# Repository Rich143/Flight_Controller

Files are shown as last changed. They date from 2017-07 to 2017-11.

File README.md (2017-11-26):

 <a href="https://scan.coverity.com/projects/rich143-flight_controller">
  
</a>

# Flight Controller #

STM32 based flight controller for quadcopter

### Board Render:
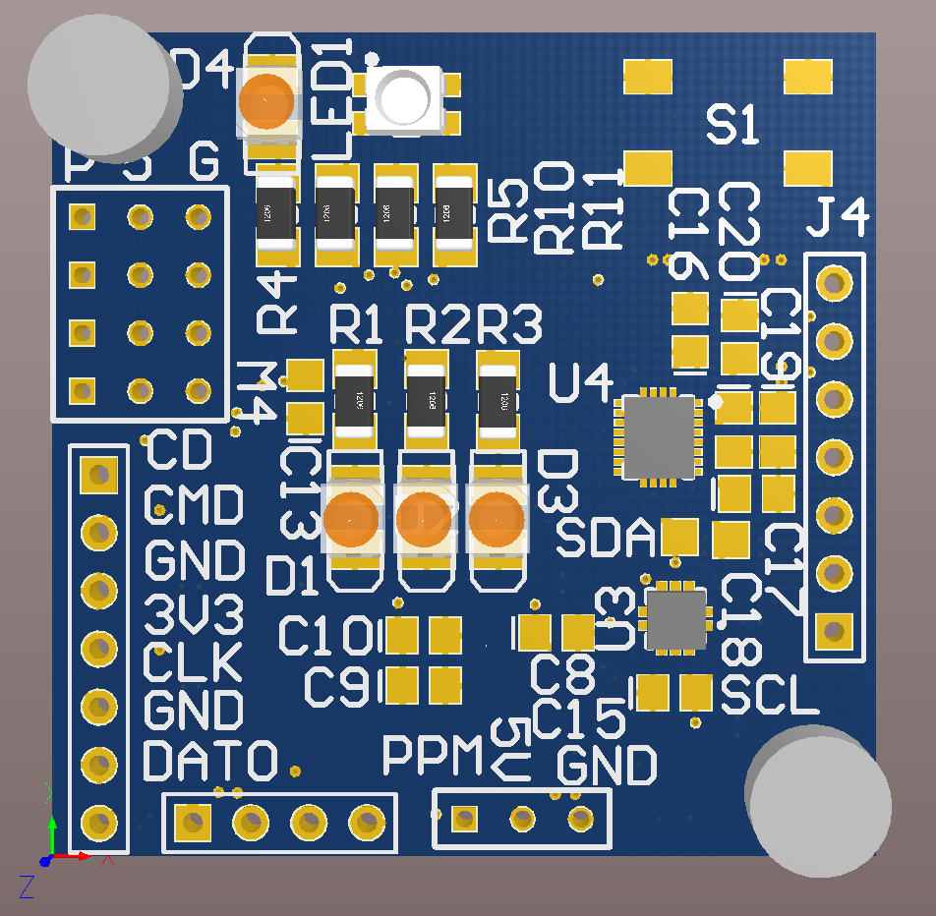
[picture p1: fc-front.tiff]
Board Render Front

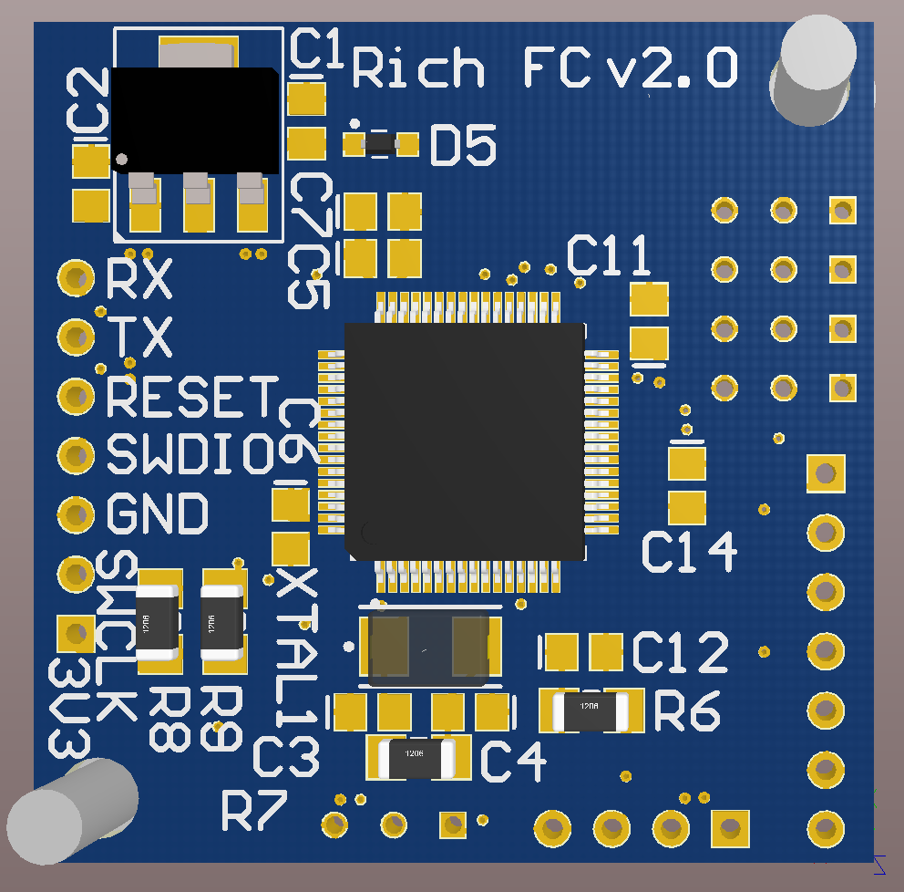
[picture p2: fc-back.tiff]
Board Render Back


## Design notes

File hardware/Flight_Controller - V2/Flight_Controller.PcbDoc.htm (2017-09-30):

Reporting Options

# File in Previous Format

Date | : | 9/21/2017
Time | : | 7:43:19 PM
Filename | : | C:\Users\Richard\Documents\Flight_Controller - V2\Flight_Controller.PcbDoc

Version | Warning

This file was generated by an earlier version of the software

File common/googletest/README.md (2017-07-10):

# Google Test #




Welcome to **Google Test**, Google's C++ test framework!

This repository is a merger of the formerly separate GoogleTest and
GoogleMock projects. These were so closely related that it makes sense to
maintain and release them together.

Please see the project page above for more information as well as the
mailing list for questions, discussions, and development.  There is
also an IRC channel on OFTC (irc.oftc.net) #gtest available.  Please
join us!

Getting started information for **Google Test** is available in the 
[Google Test Primer](googletest/docs/Primer.md) documentation.

**Google Mock** is an extension to Google Test for writing and using C++ mock
classes.  See the separate [Google Mock documentation](googlemock/README.md).

More detailed documentation for googletest (including build instructions) are
in its interior [googletest/README.md](googletest/README.md) file.

## Features ##

  * An [XUnit](https://en.wikipedia.org/wiki/XUnit) test framework.
  * Test discovery.
  * A rich set of assertions.
  * User-defined assertions.
  * Death tests.
  * Fatal and non-fatal failures.
  * Value-parameterized tests.
  * Type-parameterized tests.
  * Various options for running the tests.
  * XML test report generation.

## Platforms ##

Google test has been used on a variety of platforms:

  * Linux
  * Mac OS X
  * Windows
  * Cygwin
  * MinGW
  * Windows Mobile
  * Symbian

## Who Is Using Google Test? ##

In addition to many internal projects at Google, Google Test is also used by
the following notable projects:

  * The [Chromium projects](http://www.chromium.org/) (behind the Chrome
    browser and Chrome OS).
  * The [LLVM](http://llvm.org/) compiler.
  * [Protocol Buffers](https://github.com/google/protobuf), Google's data
    interchange format.
  * The [OpenCV](http://opencv.org/) computer vision library.

## Related Open Source Projects ##

[Google Test UI](https://github.com/ospector/gtest-gbar) is test runner that runs
your test binary, allows you to track its progress via a progress bar, and
displays a list of test failures. Clicking on one shows failure text. Google
Test UI is written in C#.

[GTest TAP Listener](https://github.com/kinow/gtest-tap-listener) is an event
listener for Google Test that implements the
[TAP protocol](https://en.wikipedia.org/wiki/Test_Anything_Protocol) for test
result output. If your test runner understands TAP, you may find it useful.

## Requirements ##

Google Test is designed to have fairly minimal requirements to build
and use with your projects, but there are some.  Currently, we support
Linux, Windows, Mac OS X, and Cygwin.  We will also make our best
effort to support other platforms (e.g. Solaris, AIX, and z/OS).
However, since core members of the Google Test project have no access
to these platforms, Google Test may have outstanding issues there.  If
you notice any problems on your platform, please notify
<googletestframework@googlegroups.com>. Patches for fixing them are
even more welcome!

### Linux Requirements ###

These are the base requirements to build and use Google Test from a source
package (as described below):

  * GNU-compatible Make or gmake
  * POSIX-standard shell
  * POSIX(-2) Regular Expressions (regex.h)
  * A C++98-standard-compliant compiler

### Windows Requirements ###

  * Microsoft Visual C++ v7.1 or newer

### Cygwin Requirements ###

  * Cygwin v1.5.25-14 or newer

### Mac OS X Requirements ###

  * Mac OS X v10.4 Tiger or newer
  * Xcode Developer Tools

### Requirements for Contributors ###

We welcome patches.  If you plan to contribute a patch, you need to
build Google Test and its own tests from a git checkout (described
below), which has further requirements:

  * [Python](https://www.python.org/) v2.3 or newer (for running some of
    the tests and re-generating certain source files from templates)
  * [CMake](https://cmake.org/) v2.6.4 or newer

## Regenerating Source Files ##

Some of Google Test's source files are generated from templates (not
in the C++ sense) using a script.
For example, the
file include/gtest/internal/gtest-type-util.h.pump is used to generate
gtest-type-util.h in the same directory.

You don't need to worry about regenerating the source files
unless you need to modify them.  You would then modify the
corresponding `.pump` files and run the '[pump.py](googletest/scripts/pump.py)'
generator script.  See the [Pump Manual](googletest/docs/PumpManual.md).

### Contributing Code ###

We welcome patches.  Please read the
[Developer's Guide](googletest/docs/DevGuide.md)
for how you can contribute. In particular, make sure you have signed
the Contributor License Agreement, or we won't be able to accept the
patch.

Happy testing!

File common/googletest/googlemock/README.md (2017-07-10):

## Google Mock ##

The Google C++ mocking framework.

### Overview ###

Google's framework for writing and using C++ mock classes.
It can help you derive better designs of your system and write better tests.

It is inspired by:

  * [jMock](http://www.jmock.org/),
  * [EasyMock](http://www.easymock.org/), and
  * [Hamcrest](http://code.google.com/p/hamcrest/),

and designed with C++'s specifics in mind.

Google mock:

  * lets you create mock classes trivially using simple macros.
  * supports a rich set of matchers and actions.
  * handles unordered, partially ordered, or completely ordered expectations.
  * is extensible by users.

We hope you find it useful!

### Features ###

  * Provides a declarative syntax for defining mocks.
  * Can easily define partial (hybrid) mocks, which are a cross of real
    and mock objects.
  * Handles functions of arbitrary types and overloaded functions.
  * Comes with a rich set of matchers for validating function arguments.
  * Uses an intuitive syntax for controlling the behavior of a mock.
  * Does automatic verification of expectations (no record-and-replay needed).
  * Allows arbitrary (partial) ordering constraints on
    function calls to be expressed,.
  * Lets a user extend it by defining new matchers and actions.
  * Does not use exceptions.
  * Is easy to learn and use.

Please see the project page above for more information as well as the
mailing list for questions, discussions, and development.  There is
also an IRC channel on OFTC (irc.oftc.net) #gtest available.  Please
join us!

Please note that code under [scripts/generator](scripts/generator/) is
from [cppclean](http://code.google.com/p/cppclean/) and released under
the Apache License, which is different from Google Mock's license.

## Getting Started ##

If you are new to the project, we suggest that you read the user
documentation in the following order:

  * Learn the [basics](../../master/googletest/docs/Primer.md) of
    Google Test, if you choose to use Google Mock with it (recommended).
  * Read [Google Mock for Dummies](../../master/googlemock/docs/ForDummies.md).
  * Read the instructions below on how to build Google Mock.

You can also watch Zhanyong's [talk](http://www.youtube.com/watch?v=sYpCyLI47rM) on Google Mock's usage and implementation.

Once you understand the basics, check out the rest of the docs:

  * [CheatSheet](../../master/googlemock/docs/CheatSheet.md) - all the commonly used stuff
    at a glance.
  * [CookBook](../../master/googlemock/docs/CookBook.md) - recipes for getting things done,
    including advanced techniques.

If you need help, please check the
[KnownIssues](docs/KnownIssues.md) and
[FrequentlyAskedQuestions](docs/FrequentlyAskedQuestions.md) before
posting a question on the
[discussion group](http://groups.google.com/group/googlemock).

### Using Google Mock Without Google Test ###

Google Mock is not a testing framework itself.  Instead, it needs a
testing framework for writing tests.  Google Mock works seamlessly
with [Google Test](http://code.google.com/p/googletest/), but
you can also use it with [any C++ testing framework](../../master/googlemock/docs/ForDummies.md#using-google-mock-with-any-testing-framework).

### Requirements for End Users ###

Google Mock is implemented on top of [Google Test](
http://github.com/google/googletest/), and depends on it.
You must use the bundled version of Google Test when using Google Mock.

You can also easily configure Google Mock to work with another testing
framework, although it will still need Google Test.  Please read
["Using_Google_Mock_with_Any_Testing_Framework"](
    ../../master/googlemock/docs/ForDummies.md#using-google-mock-with-any-testing-framework)
for instructions.

Google Mock depends on advanced C++ features and thus requires a more
modern compiler. The following are needed to use Google Mock:

#### Linux Requirements ####

  * GNU-compatible Make or "gmake"
  * POSIX-standard shell
  * POSIX(-2) Regular Expressions (regex.h)
  * C++98-standard-compliant compiler (e.g. GCC 3.4 or newer)

#### Windows Requirements ####

  * Microsoft Visual C++ 8.0 SP1 or newer

#### Mac OS X Requirements ####

  * Mac OS X 10.4 Tiger or newer
  * Developer Tools Installed

### Requirements for Contributors ###

We welcome patches. If you plan to contribute a patch, you need to
build Google Mock and its tests, which has further requirements:

  * Automake version 1.9 or newer
  * Autoconf version 2.59 or newer
  * Libtool / Libtoolize
  * Python version 2.3 or newer (for running some of the tests and
    re-generating certain source files from templates)

### Building Google Mock ###

If you have CMake available, it is recommended that you follow the
[build instructions][gtest_cmakebuild]
as described for Google Test. If are using Google Mock with an
existing CMake project, the section
[Incorporating Into An Existing CMake Project][gtest_incorpcmake]
may be of particular interest. Otherwise, the following sections
detail how to build Google Mock without CMake.

#### Preparing to Build (Unix only) ####

If you are using a Unix system and plan to use the GNU Autotools build
system to build Google Mock (described below), you'll need to
configure it now.

To prepare the Autotools build system:

    cd googlemock
    autoreconf -fvi

To build Google Mock and your tests that use it, you need to tell your
build system where to find its headers and source files.  The exact
way to do it depends on which build system you use, and is usually
straightforward.

This section shows how you can integrate Google Mock into your
existing build system.

Suppose you put Google Mock in directory `${GMOCK_DIR}` and Google Test
in `${GTEST_DIR}` (the latter is `${GMOCK_DIR}/gtest` by default).  To
build Google Mock, create a library build target (or a project as
called by Visual Studio and Xcode) to compile

    ${GTEST_DIR}/src/gtest-all.cc and ${GMOCK_DIR}/src/gmock-all.cc

with

    ${GTEST_DIR}/include and ${GMOCK_DIR}/include

in the system header search path, and

    ${GTEST_DIR} and ${GMOCK_DIR}

in the normal header search path.  Assuming a Linux-like system and gcc,
something like the following will do:

    g++ -isystem ${GTEST_DIR}/include -I${GTEST_DIR} \
        -isystem ${GMOCK_DIR}/include -I${GMOCK_DIR} \
        -pthread -c ${GTEST_DIR}/src/gtest-all.cc
    g++ -isystem ${GTEST_DIR}/include -I${GTEST_DIR} \
        -isystem ${GMOCK_DIR}/include -I${GMOCK_DIR} \
        -pthread -c ${GMOCK_DIR}/src/gmock-all.cc
    ar -rv libgmock.a gtest-all.o gmock-all.o

(We need -pthread as Google Test and Google Mock use threads.)

Next, you should compile your test source file with
${GTEST\_DIR}/include and ${GMOCK\_DIR}/include in the header search
path, and link it with gmock and any other necessary libraries:

    g++ -isystem ${GTEST_DIR}/include -isystem ${GMOCK_DIR}/include \
        -pthread path/to/your_test.cc libgmock.a -o your_test

As an example, the make/ directory contains a Makefile that you can
use to build Google Mock on systems where GNU make is available
(e.g. Linux, Mac OS X, and Cygwin).  It doesn't try to build Google
Mock's own tests.  Instead, it just builds the Google Mock library and
a sample test.  You can use it as a starting point for your own build
script.

If the default settings are correct for your environment, the
following commands should succeed:

    cd ${GMOCK_DIR}/make
    make
    ./gmock_test

If you see errors, try to tweak the contents of
[make/Makefile](make/Makefile) to make them go away.

### Windows ###

The msvc/2005 directory contains VC++ 2005 projects and the msvc/2010
directory contains VC++ 2010 projects for building Google Mock and
selected tests.

Change to the appropriate directory and run "msbuild gmock.sln" to
build the library and tests (or open the gmock.sln in the MSVC IDE).
If you want to create your own project to use with Google Mock, you'll
have to configure it to use the `gmock_config` propety sheet.  For that:

 * Open the Property Manager window (View | Other Windows | Property Manager)
 * Right-click on your project and select "Add Existing Property Sheet..."
 * Navigate to `gmock_config.vsprops` or `gmock_config.props` and select it.
 * In Project Properties | Configuration Properties | General | Additional
   Include Directories, type <path to Google Mock>/include.

### Tweaking Google Mock ###

Google Mock can be used in diverse environments.  The default
configuration may not work (or may not work well) out of the box in
some environments.  However, you can easily tweak Google Mock by
defining control macros on the compiler command line.  Generally,
these macros are named like `GTEST_XYZ` and you define them to either 1
or 0 to enable or disable a certain feature.

We list the most frequently used macros below.  For a complete list,
see file [${GTEST\_DIR}/include/gtest/internal/gtest-port.h](
../googletest/include/gtest/internal/gtest-port.h).

### Choosing a TR1 Tuple Library ###

Google Mock uses the C++ Technical Report 1 (TR1) tuple library
heavily.  Unfortunately TR1 tuple is not yet widely available with all
compilers.  The good news is that Google Test 1.4.0+ implements a
subset of TR1 tuple that's enough for Google Mock's need.  Google Mock
will automatically use that implementation when the compiler doesn't
provide TR1 tuple.

Usually you don't need to care about which tuple library Google Test
and Google Mock use.  However, if your project already uses TR1 tuple,
you need to tell Google Test and Google Mock to use the same TR1 tuple
library the rest of your project uses, or the two tuple
implementations will clash.  To do that, add

    -DGTEST_USE_OWN_TR1_TUPLE=0

to the compiler flags while compiling Google Test, Google Mock, and
your tests.  If you want to force Google Test and Google Mock to use
their own tuple library, just add

    -DGTEST_USE_OWN_TR1_TUPLE=1

to the compiler flags instead.

If you want to use Boost's TR1 tuple library with Google Mock, please
refer to the Boost website (http://www.boost.org/) for how to obtain
it and set it up.

### As a Shared Library (DLL) ###

Google Mock is compact, so most users can build and link it as a static
library for the simplicity.  Google Mock can be used as a DLL, but the
same DLL must contain Google Test as well.  See
[Google Test's README][gtest_readme]
for instructions on how to set up necessary compiler settings.

### Tweaking Google Mock ###

Most of Google Test's control macros apply to Google Mock as well.
Please see [Google Test's README][gtest_readme] for how to tweak them.

### Upgrading from an Earlier Version ###

We strive to keep Google Mock releases backward compatible.
Sometimes, though, we have to make some breaking changes for the
users' long-term benefits.  This section describes what you'll need to
do if you are upgrading from an earlier version of Google Mock.

#### Upgrading from 1.1.0 or Earlier ####

You may need to explicitly enable or disable Google Test's own TR1
tuple library.  See the instructions in section "[Choosing a TR1 Tuple
Library](../googletest/#choosing-a-tr1-tuple-library)".

#### Upgrading from 1.4.0 or Earlier ####

On platforms where the pthread library is available, Google Test and
Google Mock use it in order to be thread-safe.  For this to work, you
may need to tweak your compiler and/or linker flags.  Please see the
"[Multi-threaded Tests](../googletest#multi-threaded-tests
)" section in file Google Test's README for what you may need to do.

If you have custom matchers defined using `MatcherInterface` or
`MakePolymorphicMatcher()`, you'll need to update their definitions to
use the new matcher API (
[monomorphic](http://code.google.com/p/googlemock/wiki/CookBook#Writing_New_Monomorphic_Matchers),
[polymorphic](http://code.google.com/p/googlemock/wiki/CookBook#Writing_New_Polymorphic_Matchers)).
Matchers defined using `MATCHER()` or `MATCHER_P*()` aren't affected.

### Developing Google Mock ###

This section discusses how to make your own changes to Google Mock.

#### Testing Google Mock Itself ####

To make sure your changes work as intended and don't break existing
functionality, you'll want to compile and run Google Test's own tests.
For that you'll need Autotools.  First, make sure you have followed
the instructions above to configure Google Mock.
Then, create a build output directory and enter it.  Next,

    ${GMOCK_DIR}/configure  # try --help for more info

Once you have successfully configured Google Mock, the build steps are
standard for GNU-style OSS packages.

    make        # Standard makefile following GNU conventions
    make check  # Builds and runs all tests - all should pass.

Note that when building your project against Google Mock, you are building
against Google Test as well.  There is no need to configure Google Test
separately.

#### Contributing a Patch ####

We welcome patches.
Please read the [Developer's Guide](docs/DevGuide.md)
for how you can contribute. In particular, make sure you have signed
the Contributor License Agreement, or we won't be able to accept the
patch.

Happy testing!

[gtest_readme]: ../googletest/README.md "googletest"
[gtest_cmakebuild]:  ../googletest/README.md#using-cmake "Using CMake"
[gtest_incorpcmake]: ../googletest/README.md#incorporating-into-an-existing-cmake-project "Incorporating Into An Existing CMake Project"

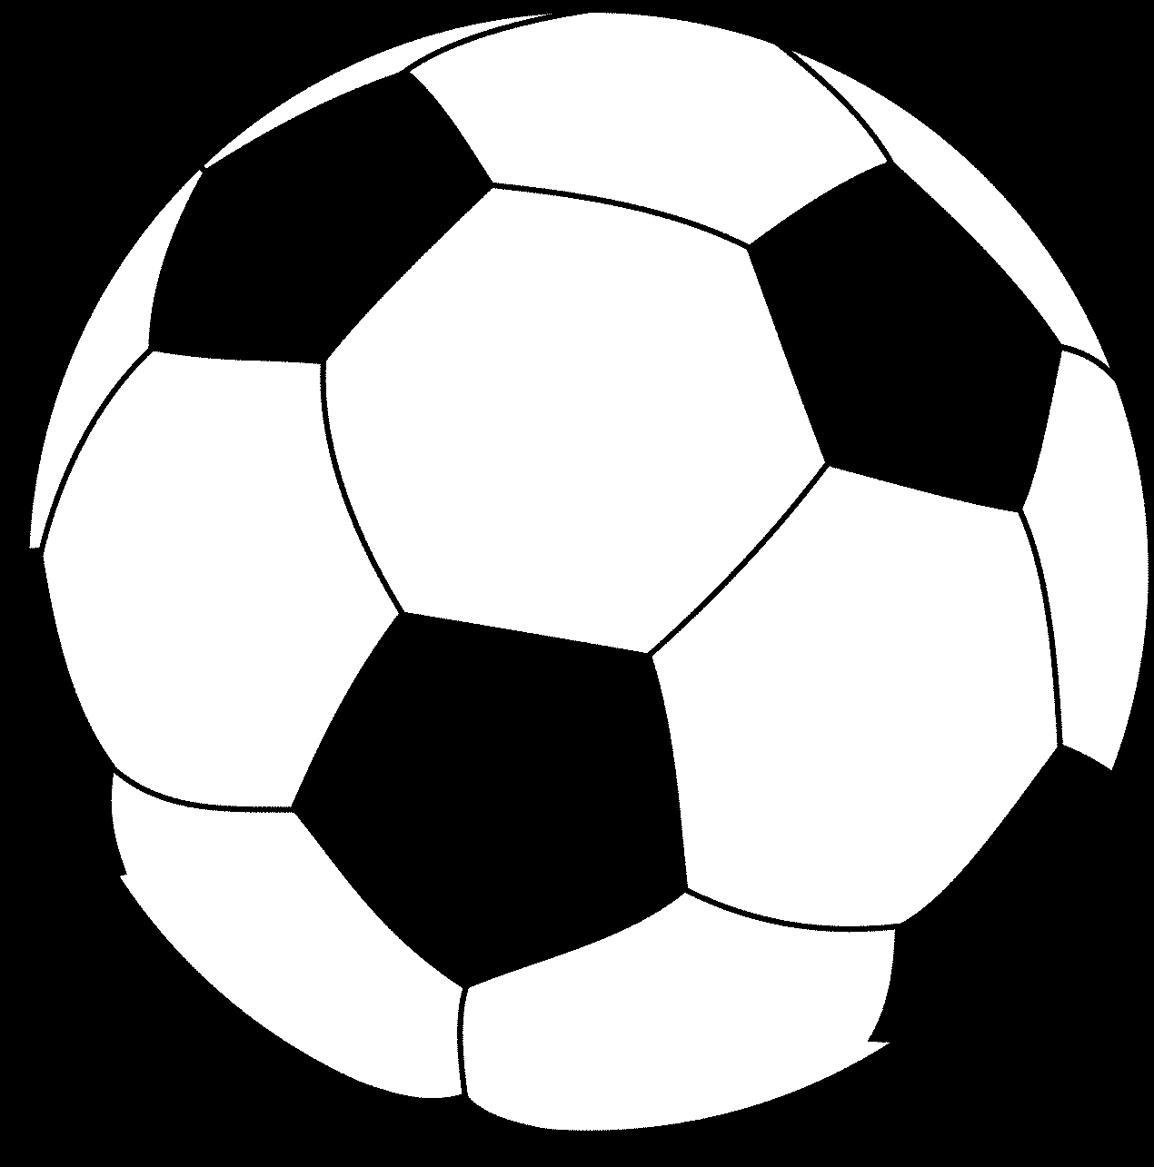
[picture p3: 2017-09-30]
hardware/Flight_Controller - V2/Soccerball.bmp

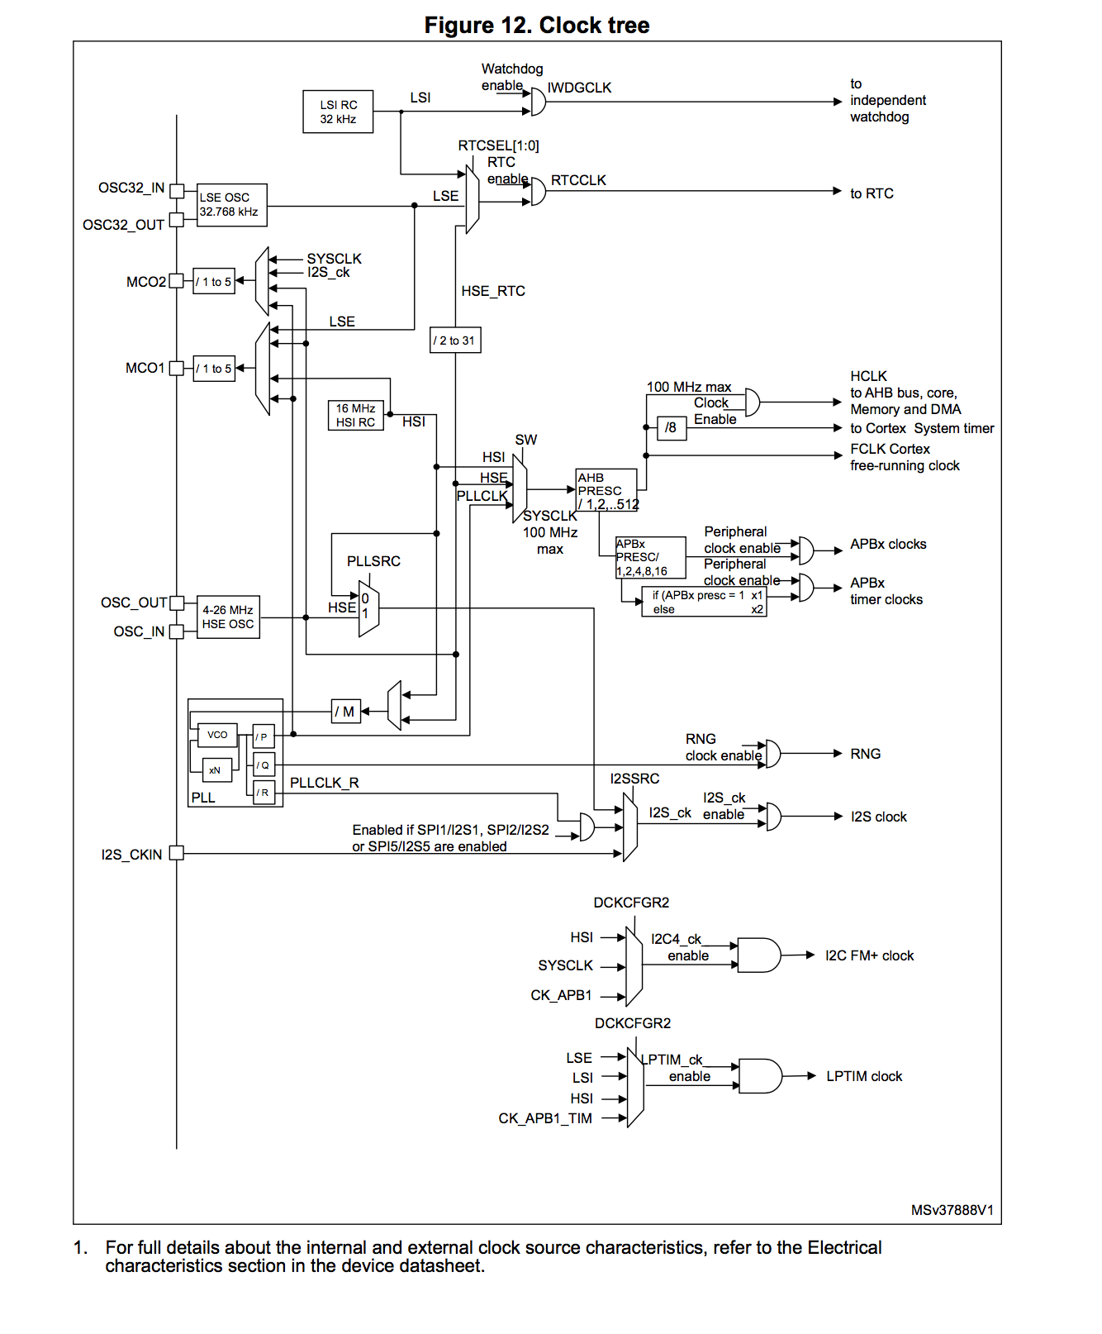
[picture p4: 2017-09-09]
docs/clock-tree.tiff

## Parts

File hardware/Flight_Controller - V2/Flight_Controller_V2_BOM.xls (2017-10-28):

Comment | Description | Designator | Footprint | LibRef | Quantity | Supplier 1 | Supplier Unit Price 1 | Supplier Currency 1 | Supplier Part Number 1 | Supplier Stock 1 | Value
Cap | Capacitor | C1, C2, C19 | C0805 | Cap | 3.0 |  | 0.0 |  |  | 0.0 | 10uF
Cap | Capacitor | C3, C4 | C0805 | Cap | 2.0 |  | 0.0 |  |  | 0.0 | 8pF
Cap | Capacitor | C5, C6, C8, C10, C11, C12, C14, C15, C16, C18, C20 | C0805 | Cap | 11.0 |  | 0.0 |  |  | 0.0 | 100nF
Cap | Capacitor | C7, C13 | C0805 | Cap | 2.0 |  | 0.0 |  |  | 0.0 | 4.7uF
Cap | Capacitor | C9 | C0805 | Cap | 1.0 |  | 0.0 |  |  | 0.0 | 1uF
Cap | Capacitor | C17 | C0805 | Cap | 1.0 |  | 0.0 |  |  | 0.0 | 10nF
150141GS73100 | Typical GREEN LED | D1 | 150141RS73100 | 150141GS73100 | 1.0 | Digikey | 0.2133 | CAD | 732-4997-1-ND | 7703.0
150141RS73100 | Typical RED LED | D2, D3, D4 | 150141RS73100 | 150141RS73100 | 3.0 | Digi-Key | 0.0 |  |  | 0.0
Schottky Diode | Diode Schottky 30V 800mA (DC) Surface Mount SOD-323 | D5 | SOD323 | DS_CUS08F30 | 1.0 | Digi-Key | 0.4517 | CAD | CUS08F30H3FCT-ND | 49875.0
Header_3x1 |  | J1 | Header_3x1 | Header_3x1 | 1.0 |  | 0.0 |  |  | 0.0
Header 4x3 |  | J2 | Header_4x3 | Header_4x3 | 1.0 |  | 0.0 |  |  | 0.0
Header 4 | Header, 4-Pin | J3 | HDR1X4 | Header 4 | 1.0 |  | 0.0 |  |  | 0.0
Header 7 | Header, 7-Pin | J4, P1 | HDR1X7 | Header 7 | 2.0 |  | 0.0 |  |  | 0.0
RGB | Wurth RGB LED 1411 pkg | LED1 | 1411LED | LED_150141M173100 | 1.0 | Digi-Key | 0.56462 | CAD | 732-4998-1-ND | 7499.0
M3_Mounting_Hole |  | M1, M2 | M3_Mounting_Hole | M3_Mounting_Hole | 2.0 |  | 0.0 |  |  | 0.0
Res | Surface Mount Resistor | R1, R2, R3, R4, R5, R6, R10, R11 | 3216[1206] | Res | 8.0 |  | 0.0 |  |  | 0.0 | 1K
Res | Surface Mount Resistor | R7 | 3216[1206] | Res | 1.0 |  | 0.0 |  |  | 0.0 | 640
Res | Surface Mount Resistor | R8, R9 | 3216[1206] | Res | 2.0 |  | 0.0 |  |  | 0.0 | 4.7k
Pushbutton |  | S1 | TactileSwitch | Pushbutton | 1.0 |  | 0.0 |  |  | 0.0
Test_point_SMD | Test Point SMD | TPS1, TPS2 | TEST_POINT_SMD | Test_point_SMD | 2.0 |  | 0.0 |  |  | 0.0
U_AZ1117EH-3.3TRG1 | IC LDO 3.3V 1A | U1 | SOT223 | U_AZ1117EH-3.3TRG1 | 1.0 | Digi-Key | 0.53953 | CAD | AZ1117EH-3.3TRG1DICT-ND | 103155.0
STM32F410RBT6 | 64-LQFP - Pinout Representation | U2 | LQFP-64 10x10mm | STM32F410RB_PINOUT | 1.0 | Digikey | 5.52076 | CAD | 497-16239-ND | 0.0
LPS25HB |  | U3 | HLGA-10L - narrow | LPS25HB | 1.0 | Digikey | 4.07784 | CAD | 497-15070-6-ND | 40076.0
LSM9DS1 |  | U4 | LGA-24 - NARROW - Long Pads | LSM9DS1 | 1.0 | Digikey | 8.0302 | CAD | 497-14946-6-ND | 0.0
NX5032GA 25MHz | NX5032GA | XTAL1 | NX5032GA | NX5032GA | 1.0 | Digikey | 0.82811 | CAD | 644-1041-1-ND | 0.0

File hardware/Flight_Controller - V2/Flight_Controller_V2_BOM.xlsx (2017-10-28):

 |  | Comment | Description | Designator | Footprint | LibRef | Quantity | Supplier 1 | Supplier Unit Price 1 | Supplier Currency 1 | Supplier Part Number 1 | Supplier Stock 1 | Value | Used | Remaining
 | T,B | Cap | Capacitor | C1, C2, C19 | C0805 | Cap | 3 |  | 0 |  |  | 0 | 10uF | 7 | 3
 | T,B | Cap | Capacitor | C3, C4 | C0805 | Cap | 2 |  | 0 |  |  | 0 | 8pF | 4 | 6
c8,c10,c15,c16,c18,c20 | c5,c6,c11,c12,c14 | Cap | Capacitor | C5, C6, C8, C10, C11, C12, C14, C15, C16, C18, C20 | C0805 | Cap | 11 |  | 0 |  |  | 0 | 100nF | 22 | 78
c13, | c7, | Cap | Capacitor | C7, C13 | C0805 | Cap | 2 |  | 0 |  |  | 0 | 4.7uF | 4 | 6
c9 |  | Cap | Capacitor | C9 | C0805 | Cap | 1 |  | 0 |  |  | 0 | 1uF | 2 | 8
c17 |  | Cap | Capacitor | C17 | C0805 | Cap | 1 |  | 0 |  |  | 0 | 10nF | 2 | 8
d1 |  | 150141GS73100 | Typical GREEN LED | D1 | 150141RS73100 | 150141GS73100 | 1 | Digikey | 0.2133 | CAD | 732-4997-1-ND | 7703 |  | 2 | 1
d2,d3,d4 |  | 150141RS73100 | Typical RED LED | D2, D3, D4 | 150141RS73100 | 150141RS73100 | 3 | Digi-Key | 0 |  |  | 0 |  | 7 | 5
d5 |  | Schottky Diode | Diode Schottky 30V 800mA (DC) Surface Mount SOD-323 | D5 | SOD323 | DS_CUS08F30 | 1 | Digi-Key | 0.4517 | CAD | CUS08F30H3FCT-ND | 49875 |  | 1 | 2
 |  | Header_3x1 |  | J1 | Header_3x1 | Header_3x1 | 1 |  | 0 |  |  | 0
 |  | Header 4x3 |  | J2 | Header_4x3 | Header_4x3 | 1 |  | 0 |  |  | 0
 |  | Header 4 | Header, 4-Pin | J3 | HDR1X4 | Header 4 | 1 |  | 0 |  |  | 0
 |  | Header 7 | Header, 7-Pin | J4, P1 | HDR1X7 | Header 7 | 2 |  | 0 |  |  | 0
led1 |  | RGB | Wurth RGB LED 1411 pkg | LED1 | 1411LED | LED_150141M173100 | 1 | Digi-Key | 0.56462 | CAD | 732-4998-1-ND | 7499 |  | 1 | 1
 |  | M3_Mounting_Hole |  | M1, M2 | M3_Mounting_Hole | M3_Mounting_Hole | 2 |  | 0 |  |  | 0
r1,r2,r3,r4,r5,r10,r11 | r6, | Res | Surface Mount Resistor | R1, R2, R3, R4, R5, R6, R10, R11 | 3216[1206] | Res | 8 |  | 0 |  |  | 0 | 1K | 16 | 9
 | r7 | Res | Surface Mount Resistor | R7 | 3216[1206] | Res | 1 |  | 0 |  |  | 0 | 640 | 2 | 8
 | r8,r9 | Res | Surface Mount Resistor | R8, R9 | 3216[1206] | Res | 2 |  | 0 |  |  | 0 | 4.7k | 4 | 6
 | s1 | Pushbutton |  | S1 | TactileSwitch | Pushbutton | 1 |  | 0 |  |  | 0
 |  | Test_point_SMD | Test Point SMD | TPS1, TPS2 | TEST_POINT_SMD | Test_point_SMD | 2 |  | 0 |  |  | 0
 | u1 | U_AZ1117EH-3.3TRG1 | IC LDO 3.3V 1A | U1 | SOT223 | U_AZ1117EH-3.3TRG1 | 1 | Digi-Key | 0.53953 | CAD | AZ1117EH-3.3TRG1DICT-ND | 103155 |  | 2 | 2
 |  | STM32F410RBT6 | 64-LQFP - Pinout Representation | U2 | LQFP-64 10x10mm | STM32F410RB_PINOUT | 1 | Digikey | 5.52076 | CAD | 497-16239-ND | 0
 |  | LPS25HB |  | U3 | HLGA-10L - narrow | LPS25HB | 1 | Digikey | 4.07784 | CAD | 497-15070-6-ND | 40076
 |  | LSM9DS1 |  | U4 | LGA-24 - NARROW - Long Pads | LSM9DS1 | 1 | Digikey | 8.0302 | CAD | 497-14946-6-ND | 0
 | xtal1 | NX5032GA 25MHz | NX5032GA | XTAL1 | NX5032GA | NX5032GA | 1 | Digikey | 0.82811 | CAD | 644-1041-1-ND | 0

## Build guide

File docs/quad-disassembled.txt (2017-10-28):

Steps taken to disassemble quad for testing:
-took off top plate
-cut off zip tie holding antenna in place
-unplugged rc connector from receiver to fc, goes in pins on top from unlabelled, circle, and pin with label 1
-unplugged esc connectors from fc, goes into first for from front, in order back right, front right, back left, front left
-unplugged vtx connector
-unplugged batt monitor, purple cable that goes to +Batt
-unplugged beeper, blue cable goes to plus side, adjacent to batt monitor, green goes to minus side
-spare parts in container in workbench

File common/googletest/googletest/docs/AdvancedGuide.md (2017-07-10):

Now that you have read [Primer](Primer.md) and learned how to write tests
using Google Test, it's time to learn some new tricks. This document
will show you more assertions as well as how to construct complex
failure messages, propagate fatal failures, reuse and speed up your
test fixtures, and use various flags with your tests.

# More Assertions #

This section covers some less frequently used, but still significant,
assertions.

## Explicit Success and Failure ##

These three assertions do not actually test a value or expression. Instead,
they generate a success or failure directly. Like the macros that actually
perform a test, you may stream a custom failure message into the them.

| `SUCCEED();` |
|:-------------|

Generates a success. This does NOT make the overall test succeed. A test is
considered successful only if none of its assertions fail during its execution.

Note: `SUCCEED()` is purely documentary and currently doesn't generate any
user-visible output. However, we may add `SUCCEED()` messages to Google Test's
output in the future.

| `FAIL();`  | `ADD_FAILURE();` | `ADD_FAILURE_AT("`_file\_path_`", `_line\_number_`);` |
|:---|:---|:---|

`FAIL()` generates a fatal failure, while `ADD_FAILURE()` and `ADD_FAILURE_AT()` generate a nonfatal
failure. These are useful when control flow, rather than a Boolean expression,
deteremines the test's success or failure. For example, you might want to write
something like:

```
switch(expression) {
  case 1: ... some checks ...
  case 2: ... some other checks
  ...
  default: FAIL() << "We shouldn't get here.";
}
```

Note: you can only use `FAIL()` in functions that return `void`. See the [Assertion Placement section](#assertion-placement) for more information.

_Availability_: Linux, Windows, Mac.

## Exception Assertions ##

These are for verifying that a piece of code throws (or does not
throw) an exception of the given type:

| **Fatal assertion** | **Nonfatal assertion** | **Verifies** |
|:---|:---|:---|
| `ASSERT_THROW(`_statement_, _exception\_type_`);`  | `EXPECT_THROW(`_statement_, _exception\_type_`);`  | _statement_ throws an exception of the given type  |
| `ASSERT_ANY_THROW(`_statement_`);` | `EXPECT_ANY_THROW(`_statement_`);` | _statement_ throws an exception of any type |
| `ASSERT_NO_THROW(`_statement_`);` | `EXPECT_NO_THROW(`_statement_`);` | _statement_ doesn't throw any exception |

Examples:

```
ASSERT_THROW(Foo(5), bar_exception);

EXPECT_NO_THROW({
  int n = 5;
  Bar(&n);
});
```

_Availability_: Linux, Windows, Mac; since version 1.1.0.

## Predicate Assertions for Better Error Messages ##

Even though Google Test has a rich set of assertions, they can never be
complete, as it's impossible (nor a good idea) to anticipate all the scenarios
a user might run into. Therefore, sometimes a user has to use `EXPECT_TRUE()`
to check a complex expression, for lack of a better macro. This has the problem
of not showing you the values of the parts of the expression, making it hard to
understand what went wrong. As a workaround, some users choose to construct the
failure message by themselves, streaming it into `EXPECT_TRUE()`. However, this
is awkward especially when the expression has side-effects or is expensive to
evaluate.

Google Test gives you three different options to solve this problem:

### Using an Existing Boolean Function ###

If you already have a function or a functor that returns `bool` (or a type
that can be implicitly converted to `bool`), you can use it in a _predicate
assertion_ to get the function arguments printed for free:

| **Fatal assertion** | **Nonfatal assertion** | **Verifies** |
|:---|:---|:---|
| `ASSERT_PRED1(`_pred1, val1_`);` | `EXPECT_PRED1(`_pred1, val1_`);` | _pred1(val1)_ returns true |
| `ASSERT_PRED2(`_pred2, val1, val2_`);` | `EXPECT_PRED2(`_pred2, val1, val2_`);` |  _pred2(val1, val2)_ returns true |
|  ... | ... | ... |

In the above, _predn_ is an _n_-ary predicate function or functor, where
_val1_, _val2_, ..., and _valn_ are its arguments. The assertion succeeds
if the predicate returns `true` when applied to the given arguments, and fails
otherwise. When the assertion fails, it prints the value of each argument. In
either case, the arguments are evaluated exactly once.

Here's an example. Given

```
// Returns true iff m and n have no common divisors except 1.
bool MutuallyPrime(int m, int n) { ... }
const int a = 3;
const int b = 4;
const int c = 10;
```

the assertion `EXPECT_PRED2(MutuallyPrime, a, b);` will succeed, while the
assertion `EXPECT_PRED2(MutuallyPrime, b, c);` will fail with the message

<pre>
!MutuallyPrime(b, c) is false, where<br>
b is 4<br>
c is 10<br>
</pre>

**Notes:**

  1. If you see a compiler error "no matching function to call" when using `ASSERT_PRED*` or `EXPECT_PRED*`, please see [this FAQ](FAQ.md#the-compiler-complains-no-matching-function-to-call-when-i-use-assert_predn-how-do-i-fix-it) for how to resolve it.
  1. Currently we only provide predicate assertions of arity <= 5. If you need a higher-arity assertion, let us know.

_Availability_: Linux, Windows, Mac

### Using a Function That Returns an AssertionResult ###

While `EXPECT_PRED*()` and friends are handy for a quick job, the
syntax is not satisfactory: you have to use different macros for
different arities, and it feels more like Lisp than C++.  The
`::testing::AssertionResult` class solves this problem.

An `AssertionResult` object represents the result of an assertion
(whether it's a success or a failure, and an associated message).  You
can create an `AssertionResult` using one of these factory
functions:

```
namespace testing {

// Returns an AssertionResult object to indicate that an assertion has
// succeeded.
AssertionResult AssertionSuccess();

// Returns an AssertionResult object to indicate that an assertion has
// failed.
AssertionResult AssertionFailure();

}
```

You can then use the `<<` operator to stream messages to the
`AssertionResult` object.

To provide more readable messages in Boolean assertions
(e.g. `EXPECT_TRUE()`), write a predicate function that returns
`AssertionResult` instead of `bool`. For example, if you define
`IsEven()` as:

```
::testing::AssertionResult IsEven(int n) {
  if ((n % 2) == 0)
    return ::testing::AssertionSuccess();
  else
    return ::testing::AssertionFailure() << n << " is odd";
}
```

instead of:

```
bool IsEven(int n) {
  return (n % 2) == 0;
}
```

the failed assertion `EXPECT_TRUE(IsEven(Fib(4)))` will print:

<pre>
Value of: IsEven(Fib(4))<br>
Actual: false (*3 is odd*)<br>
Expected: true<br>
</pre>

instead of a more opaque

<pre>
Value of: IsEven(Fib(4))<br>
Actual: false<br>
Expected: true<br>
</pre>

If you want informative messages in `EXPECT_FALSE` and `ASSERT_FALSE`
as well, and are fine with making the predicate slower in the success
case, you can supply a success message:

```
::testing::AssertionResult IsEven(int n) {
  if ((n % 2) == 0)
    return ::testing::AssertionSuccess() << n << " is even";
  else
    return ::testing::AssertionFailure() << n << " is odd";
}
```

Then the statement `EXPECT_FALSE(IsEven(Fib(6)))` will print

<pre>
Value of: IsEven(Fib(6))<br>
Actual: true (8 is even)<br>
Expected: false<br>
</pre>

_Availability_: Linux, Windows, Mac; since version 1.4.1.

### Using a Predicate-Formatter ###

If you find the default message generated by `(ASSERT|EXPECT)_PRED*` and
`(ASSERT|EXPECT)_(TRUE|FALSE)` unsatisfactory, or some arguments to your
predicate do not support streaming to `ostream`, you can instead use the
following _predicate-formatter assertions_ to _fully_ customize how the
message is formatted:

| **Fatal assertion** | **Nonfatal assertion** | **Verifies** |
|:---|:---|:---|
| `ASSERT_PRED_FORMAT1(`_pred\_format1, val1_`);` | `EXPECT_PRED_FORMAT1(`_pred\_format1, val1_`);` | _pred\_format1(val1)_ is successful |
| `ASSERT_PRED_FORMAT2(`_pred\_format2, val1, val2_`);` | `EXPECT_PRED_FORMAT2(`_pred\_format2, val1, val2_`);` | _pred\_format2(val1, val2)_ is successful |
| `...` | `...` | `...` |

The difference between this and the previous two groups of macros is that instead of
a predicate, `(ASSERT|EXPECT)_PRED_FORMAT*` take a _predicate-formatter_
(_pred\_formatn_), which is a function or functor with the signature:

`::testing::AssertionResult PredicateFormattern(const char* `_expr1_`, const char* `_expr2_`, ... const char* `_exprn_`, T1 `_val1_`, T2 `_val2_`, ... Tn `_valn_`);`

where _val1_, _val2_, ..., and _valn_ are the values of the predicate
arguments, and _expr1_, _expr2_, ..., and _exprn_ are the corresponding
expressions as they appear in the source code. The types `T1`, `T2`, ..., and
`Tn` can be either value types or reference types. For example, if an
argument has type `Foo`, you can declare it as either `Foo` or `const Foo&`,
whichever is appropriate.

A predicate-formatter returns a `::testing::AssertionResult` object to indicate
whether the assertion has succeeded or not. The only way to create such an
object is to call one of these factory functions:

As an example, let's improve the failure message in the previous example, which uses `EXPECT_PRED2()`:

```
// Returns the smallest prime common divisor of m and n,
// or 1 when m and n are mutually prime.
int SmallestPrimeCommonDivisor(int m, int n) { ... }

// A predicate-formatter for asserting that two integers are mutually prime.
::testing::AssertionResult AssertMutuallyPrime(const char* m_expr,
                                               const char* n_expr,
                                               int m,
                                               int n) {
  if (MutuallyPrime(m, n))
    return ::testing::AssertionSuccess();

  return ::testing::AssertionFailure()
      << m_expr << " and " << n_expr << " (" << m << " and " << n
      << ") are not mutually prime, " << "as they have a common divisor "
      << SmallestPrimeCommonDivisor(m, n);
}
```

With this predicate-formatter, we can use

```
EXPECT_PRED_FORMAT2(AssertMutuallyPrime, b, c);
```

to generate the message

<pre>
b and c (4 and 10) are not mutually prime, as they have a common divisor 2.<br>
</pre>

As you may have realized, many of the assertions we introduced earlier are
special cases of `(EXPECT|ASSERT)_PRED_FORMAT*`. In fact, most of them are
indeed defined using `(EXPECT|ASSERT)_PRED_FORMAT*`.

_Availability_: Linux, Windows, Mac.

## Floating-Point Comparison ##

Comparing floating-point numbers is tricky. Due to round-off errors, it is
very unlikely that two floating-points will match exactly. Therefore,
`ASSERT_EQ` 's naive comparison usually doesn't work. And since floating-points
can have a wide value range, no single fixed error bound works. It's better to
compare by a fixed relative error bound, except for values close to 0 due to
the loss of precision there.

In general, for floating-point comparison to make sense, the user needs to
carefully choose the error bound. If they don't want or care to, comparing in
terms of Units in the Last Place (ULPs) is a good default, and Google Test
provides assertions to do this. Full details about ULPs are quite long; if you
want to learn more, see
[this article on float comparison](http://www.cygnus-software.com/papers/comparingfloats/comparingfloats.htm).

### Floating-Point Macros ###

| **Fatal assertion** | **Nonfatal assertion** | **Verifies** |
|:---|:---|:---|
| `ASSERT_FLOAT_EQ(`_val1, val2_`);`  | `EXPECT_FLOAT_EQ(`_val1, val2_`);` | the two `float` values are almost equal |
| `ASSERT_DOUBLE_EQ(`_val1, val2_`);` | `EXPECT_DOUBLE_EQ(`_val1, val2_`);` | the two `double` values are almost equal |

By "almost equal", we mean the two values are within 4 ULP's from each
other.

The following assertions allow you to choose the acceptable error bound:

| **Fatal assertion** | **Nonfatal assertion** | **Verifies** |
|:---|:---|:---|
| `ASSERT_NEAR(`_val1, val2, abs\_error_`);` | `EXPECT_NEAR`_(val1, val2, abs\_error_`);` | the difference between _val1_ and _val2_ doesn't exceed the given absolute error |

_Availability_: Linux, Windows, Mac.

### Floating-Point Predicate-Format Functions ###

Some floating-point operations are useful, but not that often used. In order
to avoid an explosion of new macros, we provide them as predicate-format
functions that can be used in predicate assertion macros (e.g.
`EXPECT_PRED_FORMAT2`, etc).

```
EXPECT_PRED_FORMAT2(::testing::FloatLE, val1, val2);
EXPECT_PRED_FORMAT2(::testing::DoubleLE, val1, val2);
```

Verifies that _val1_ is less than, or almost equal to, _val2_. You can
replace `EXPECT_PRED_FORMAT2` in the above table with `ASSERT_PRED_FORMAT2`.

_Availability_: Linux, Windows, Mac.

## Windows HRESULT assertions ##

These assertions test for `HRESULT` success or failure.

| **Fatal assertion** | **Nonfatal assertion** | **Verifies** |
|:---|:---|:---|
| `ASSERT_HRESULT_SUCCEEDED(`_expression_`);` | `EXPECT_HRESULT_SUCCEEDED(`_expression_`);` | _expression_ is a success `HRESULT` |
| `ASSERT_HRESULT_FAILED(`_expression_`);` | `EXPECT_HRESULT_FAILED(`_expression_`);` | _expression_ is a failure `HRESULT` |

The generated output contains the human-readable error message
associated with the `HRESULT` code returned by _expression_.

You might use them like this:

```
CComPtr shell;
ASSERT_HRESULT_SUCCEEDED(shell.CoCreateInstance(L"Shell.Application"));
CComVariant empty;
ASSERT_HRESULT_SUCCEEDED(shell->ShellExecute(CComBSTR(url), empty, empty, empty, empty));
```

_Availability_: Windows.

## Type Assertions ##

You can call the function
```
::testing::StaticAssertTypeEq<T1, T2>();
```
to assert that types `T1` and `T2` are the same.  The function does
nothing if the assertion is satisfied.  If the types are different,
the function call will fail to compile, and the compiler error message
will likely (depending on the compiler) show you the actual values of
`T1` and `T2`.  This is mainly useful inside template code.

_Caveat:_ When used inside a member function of a class template or a
function template, `StaticAssertTypeEq<T1, T2>()` is effective _only if_
the function is instantiated.  For example, given:
```
template <typename T> class Foo {
 public:
  void Bar() { ::testing::StaticAssertTypeEq<int, T>(); }
};
```
the code:
```
void Test1() { Foo<bool> foo; }
```
will _not_ generate a compiler error, as `Foo<bool>::Bar()` is never
actually instantiated.  Instead, you need:
```
void Test2() { Foo<bool> foo; foo.Bar(); }
```
to cause a compiler error.

_Availability:_ Linux, Windows, Mac; since version 1.3.0.

## Assertion Placement ##

You can use assertions in any C++ function. In particular, it doesn't
have to be a method of the test fixture class. The one constraint is
that assertions that generate a fatal failure (`FAIL*` and `ASSERT_*`)
can only be used in void-returning functions. This is a consequence of
Google Test not using exceptions. By placing it in a non-void function
you'll get a confusing compile error like
`"error: void value not ignored as it ought to be"`.

If you need to use assertions in a function that returns non-void, one option
is to make the function return the value in an out parameter instead. For
example, you can rewrite `T2 Foo(T1 x)` to `void Foo(T1 x, T2* result)`. You
need to make sure that `*result` contains some sensible value even when the
function returns prematurely. As the function now returns `void`, you can use
any assertion inside of it.

If changing the function's type is not an option, you should just use
assertions that generate non-fatal failures, such as `ADD_FAILURE*` and
`EXPECT_*`.

_Note_: Constructors and destructors are not considered void-returning
functions, according to the C++ language specification, and so you may not use
fatal assertions in them. You'll get a compilation error if you try. A simple
workaround is to transfer the entire body of the constructor or destructor to a
private void-returning method. However, you should be aware that a fatal
assertion failure in a constructor does not terminate the current test, as your
intuition might suggest; it merely returns from the constructor early, possibly
leaving your object in a partially-constructed state. Likewise, a fatal
assertion failure in a destructor may leave your object in a
partially-destructed state. Use assertions carefully in these situations!

# Teaching Google Test How to Print Your Values #

When a test assertion such as `EXPECT_EQ` fails, Google Test prints the
argument values to help you debug.  It does this using a
user-extensible value printer.

This printer knows how to print built-in C++ types, native arrays, STL
containers, and any type that supports the `<<` operator.  For other
types, it prints the raw bytes in the value and hopes that you the
user can figure it out.

As mentioned earlier, the printer is _extensible_.  That means
you can teach it to do a better job at printing your particular type
than to dump the bytes.  To do that, define `<<` for your type:

```
#include <iostream>

namespace foo {

class Bar { ... };  // We want Google Test to be able to print instances of this.

// It's important that the << operator is defined in the SAME
// namespace that defines Bar.  C++'s look-up rules rely on that.
::std::ostream& operator<<(::std::ostream& os, const Bar& bar) {
  return os << bar.DebugString();  // whatever needed to print bar to os
}

}  // namespace foo
```

Sometimes, this might not be an option: your team may consider it bad
style to have a `<<` operator for `Bar`, or `Bar` may already have a
`<<` operator that doesn't do what you want (and you cannot change
it).  If so, you can instead define a `PrintTo()` function like this:

```
#include <iostream>

namespace foo {

class Bar { ... };

// It's important that PrintTo() is defined in the SAME
// namespace that defines Bar.  C++'s look-up rules rely on that.
void PrintTo(const Bar& bar, ::std::ostream* os) {
  *os << bar.DebugString();  // whatever needed to print bar to os
}

}  // namespace foo
```

If you have defined both `<<` and `PrintTo()`, the latter will be used
when Google Test is concerned.  This allows you to customize how the value
appears in Google Test's output without affecting code that relies on the
behavior of its `<<` operator.

If you want to print a value `x` using Google Test's value printer
yourself, just call `::testing::PrintToString(`_x_`)`, which
returns an `std::string`:

```
vector<pair<Bar, int> > bar_ints = GetBarIntVector();

EXPECT_TRUE(IsCorrectBarIntVector(bar_ints))
    << "bar_ints = " << ::testing::PrintToString(bar_ints);
```

# Death Tests #

In many applications, there are assertions that can cause application failure
if a condition is not met. These sanity checks, which ensure that the program
is in a known good state, are there to fail at the earliest possible time after
some program state is corrupted. If the assertion checks the wrong condition,
then the program may proceed in an erroneous state, which could lead to memory
corruption, security holes, or worse. Hence it is vitally important to test
that such assertion statements work as expected.

Since these precondition checks cause the processes to die, we call such tests
_death tests_. More generally, any test that checks that a program terminates
(except by throwing an exception) in an expected fashion is also a death test.

Note that if a piece of code throws an exception, we don't consider it "death"
for the purpose of death tests, as the caller of the code could catch the exception
and avoid the crash. If you want to verify exceptions thrown by your code,
see [Exception Assertions](#exception-assertions).

If you want to test `EXPECT_*()/ASSERT_*()` failures in your test code, see [Catching Failures](#catching-failures).

## How to Write a Death Test ##

Google Test has the following macros to support death tests:

| **Fatal assertion** | **Nonfatal assertion** | **Verifies** |
|:---|:---|:---|
| `ASSERT_DEATH(`_statement, regex_`);` | `EXPECT_DEATH(`_statement, regex_`);` | _statement_ crashes with the given error |
| `ASSERT_DEATH_IF_SUPPORTED(`_statement, regex_`);` | `EXPECT_DEATH_IF_SUPPORTED(`_statement, regex_`);` | if death tests are supported, verifies that _statement_ crashes with the given error; otherwise verifies nothing |
| `ASSERT_EXIT(`_statement, predicate, regex_`);` | `EXPECT_EXIT(`_statement, predicate, regex_`);` |_statement_ exits with the given error and its exit code matches _predicate_ |

where _statement_ is a statement that is expected to cause the process to
die, _predicate_ is a function or function object that evaluates an integer
exit status, and _regex_ is a regular expression that the stderr output of
_statement_ is expected to match. Note that _statement_ can be _any valid
statement_ (including _compound statement_) and doesn't have to be an
expression.

As usual, the `ASSERT` variants abort the current test function, while the
`EXPECT` variants do not.

**Note:** We use the word "crash" here to mean that the process
terminates with a _non-zero_ exit status code.  There are two
possibilities: either the process has called `exit()` or `_exit()`
with a non-zero value, or it may be killed by a signal.

This means that if _statement_ terminates the process with a 0 exit
code, it is _not_ considered a crash by `EXPECT_DEATH`.  Use
`EXPECT_EXIT` instead if this is the case, or if you want to restrict
the exit code more precisely.

A predicate here must accept an `int` and return a `bool`. The death test
succeeds only if the predicate returns `true`. Google Test defines a few
predicates that handle the most common cases:

```
::testing::ExitedWithCode(exit_code)
```

This expression is `true` if the program exited normally with the given exit
code.

```
::testing::KilledBySignal(signal_number)  // Not available on Windows.
```

This expression is `true` if the program was killed by the given signal.

The `*_DEATH` macros are convenient wrappers for `*_EXIT` that use a predicate
that verifies the process' exit code is non-zero.

Note that a death test only cares about three things:

  1. does _statement_ abort or exit the process?
  1. (in the case of `ASSERT_EXIT` and `EXPECT_EXIT`) does the exit status satisfy _predicate_?  Or (in the case of `ASSERT_DEATH` and `EXPECT_DEATH`) is the exit status non-zero?  And
  1. does the stderr output match _regex_?

In particular, if _statement_ generates an `ASSERT_*` or `EXPECT_*` failure, it will **not** cause the death test to fail, as Google Test assertions don't abort the process.

To write a death test, simply use one of the above macros inside your test
function. For example,

```
TEST(MyDeathTest, Foo) {
  // This death test uses a compound statement.
  ASSERT_DEATH({ int n = 5; Foo(&n); }, "Error on line .* of Foo()");
}
TEST(MyDeathTest, NormalExit) {
  EXPECT_EXIT(NormalExit(), ::testing::ExitedWithCode(0), "Success");
}
TEST(MyDeathTest, KillMyself) {
  EXPECT_EXIT(KillMyself(), ::testing::KilledBySignal(SIGKILL), "Sending myself unblockable signal");
}
```

verifies that:

  * calling `Foo(5)` causes the process to die with the given error message,
  * calling `NormalExit()` causes the process to print `"Success"` to stderr and exit with exit code 0, and
  * calling `KillMyself()` kills the process with signal `SIGKILL`.

The test function body may contain other assertions and statements as well, if
necessary.

_Important:_ We strongly recommend you to follow the convention of naming your
test case (not test) `*DeathTest` when it contains a death test, as
demonstrated in the above example. The `Death Tests And Threads` section below
explains why.

If a test fixture class is shared by normal tests and death tests, you
can use typedef to introduce an alias for the fixture class and avoid
duplicating its code:
```
class FooTest : public ::testing::Test { ... };

typedef FooTest FooDeathTest;

TEST_F(FooTest, DoesThis) {
  // normal test
}

TEST_F(FooDeathTest, DoesThat) {
  // death test
}
```

_Availability:_ Linux, Windows (requires MSVC 8.0 or above), Cygwin, and Mac (the latter three are supported since v1.3.0).  `(ASSERT|EXPECT)_DEATH_IF_SUPPORTED` are new in v1.4.0.

## Regular Expression Syntax ##

On POSIX systems (e.g. Linux, Cygwin, and Mac), Google Test uses the
[POSIX extended regular expression](http://www.opengroup.org/onlinepubs/009695399/basedefs/xbd_chap09.html#tag_09_04)
syntax in death tests. To learn about this syntax, you may want to read this [Wikipedia entry](http://en.wikipedia.org/wiki/Regular_expression#POSIX_Extended_Regular_Expressions).

On Windows, Google Test uses its own simple regular expression
implementation. It lacks many features you can find in POSIX extended
regular expressions.  For example, we don't support union (`"x|y"`),
grouping (`"(xy)"`), brackets (`"[xy]"`), and repetition count
(`"x{5,7}"`), among others. Below is what we do support (Letter `A` denotes a
literal character, period (`.`), or a single `\\` escape sequence; `x`
and `y` denote regular expressions.):

| `c` | matches any literal character `c` |
|:----|:---|
| `\\d` | matches any decimal digit |
| `\\D` | matches any character that's not a decimal digit |
| `\\f` | matches `\f` |
| `\\n` | matches `\n` |
| `\\r` | matches `\r` |
| `\\s` | matches any ASCII whitespace, including `\n` |
| `\\S` | matches any character that's not a whitespace |
| `\\t` | matches `\t` |
| `\\v` | matches `\v` |
| `\\w` | matches any letter, `_`, or decimal digit |
| `\\W` | matches any character that `\\w` doesn't match |
| `\\c` | matches any literal character `c`, which must be a punctuation |
| `\\.` | matches the `.` character |
| `.` | matches any single character except `\n` |
| `A?` | matches 0 or 1 occurrences of `A` |
| `A*` | matches 0 or many occurrences of `A` |
| `A+` | matches 1 or many occurrences of `A` |
| `^` | matches the beginning of a string (not that of each line) |
| `$` | matches the end of a string (not that of each line) |
| `xy` | matches `x` followed by `y` |

To help you determine which capability is available on your system,
Google Test defines macro `GTEST_USES_POSIX_RE=1` when it uses POSIX
extended regular expressions, or `GTEST_USES_SIMPLE_RE=1` when it uses
the simple version.  If you want your death tests to work in both
cases, you can either `#if` on these macros or use the more limited
syntax only.

## How It Works ##

Under the hood, `ASSERT_EXIT()` spawns a new process and executes the
death test statement in that process. The details of of how precisely
that happens depend on the platform and the variable
`::testing::GTEST_FLAG(death_test_style)` (which is initialized from the
command-line flag `--gtest_death_test_style`).

  * On POSIX systems, `fork()` (or `clone()` on Linux) is used to spawn the child, after which:
    * If the variable's value is `"fast"`, the death test statement is immediately executed.
    * If the variable's value is `"threadsafe"`, the child process re-executes the unit test binary just as it was originally invoked, but with some extra flags to cause just the single death test under consideration to be run.
  * On Windows, the child is spawned using the `CreateProcess()` API, and re-executes the binary to cause just the single death test under consideration to be run - much like the `threadsafe` mode on POSIX.

Other values for the variable are illegal and will cause the death test to
fail. Currently, the flag's default value is `"fast"`. However, we reserve the
right to change it in the future. Therefore, your tests should not depend on
this.

In either case, the parent process waits for the child process to complete, and checks that

  1. the child's exit status satisfies the predicate, and
  1. the child's stderr matches the regular expression.

If the death test statement runs to completion without dying, the child
process will nonetheless terminate, and the assertion fails.

## Death Tests And Threads ##

The reason for the two death test styles has to do with thread safety. Due to
well-known problems with forking in the presence of threads, death tests should
be run in a single-threaded context. Sometimes, however, it isn't feasible to
arrange that kind of environment. For example, statically-initialized modules
may start threads before main is ever reached. Once threads have been created,
it may be difficult or impossible to clean them up.

Google Test has three features intended to raise awareness of threading issues.

  1. A warning is emitted if multiple threads are running when a death test is encountered.
  1. Test cases with a name ending in "DeathTest" are run before all other tests.
  1. It uses `clone()` instead of `fork()` to spawn the child process on Linux (`clone()` is not available on Cygwin and Mac), as `fork()` is more likely to cause the child to hang when the parent process has multiple threads.

It's perfectly fine to create threads inside a death test statement; they are
executed in a separate process and cannot affect the parent.

## Death Test Styles ##

The "threadsafe" death test style was introduced in order to help mitigate the
risks of testing in a possibly multithreaded environment. It trades increased
test execution time (potentially dramatically so) for improved thread safety.
We suggest using the faster, default "fast" style unless your test has specific
problems with it.

You can choose a particular style of death tests by setting the flag
programmatically:

```
::testing::FLAGS_gtest_death_test_style = "threadsafe";
```

You can do this in `main()` to set the style for all death tests in the
binary, or in individual tests. Recall that flags are saved before running each
test and restored afterwards, so you need not do that yourself. For example:

```
TEST(MyDeathTest, TestOne) {
  ::testing::FLAGS_gtest_death_test_style = "threadsafe";
  // This test is run in the "threadsafe" style:
  ASSERT_DEATH(ThisShouldDie(), "");
}

TEST(MyDeathTest, TestTwo) {
  // This test is run in the "fast" style:
  ASSERT_DEATH(ThisShouldDie(), "");
}

int main(int argc, char** argv) {
  ::testing::InitGoogleTest(&argc, argv);
  ::testing::FLAGS_gtest_death_test_style = "fast";
  return RUN_ALL_TESTS();
}
```

## Caveats ##

The _statement_ argument of `ASSERT_EXIT()` can be any valid C++ statement.
If it leaves the current function via a `return` statement or by throwing an exception,
the death test is considered to have failed.  Some Google Test macros may return
from the current function (e.g. `ASSERT_TRUE()`), so be sure to avoid them in _statement_.

Since _statement_ runs in the child process, any in-memory side effect (e.g.
modifying a variable, releasing memory, etc) it causes will _not_ be observable
in the parent process. In particular, if you release memory in a death test,
your program will fail the heap check as the parent process will never see the
memory reclaimed. To solve this problem, you can

  1. try not to free memory in a death test;
  1. free the memory again in the parent process; or
  1. do not use the heap checker in your program.

Due to an implementation detail, you cannot place multiple death test
assertions on the same line; otherwise, compilation will fail with an unobvious
error message.

Despite the improved thread safety afforded by the "threadsafe" style of death
test, thread problems such as deadlock are still possible in the presence of
handlers registered with `pthread_atfork(3)`.

# Using Assertions in Sub-routines #

## Adding Traces to Assertions ##

If a test sub-routine is called from several places, when an assertion
inside it fails, it can be hard to tell which invocation of the
sub-routine the failure is from.  You can alleviate this problem using
extra logging or custom failure messages, but that usually clutters up
your tests. A better solution is to use the `SCOPED_TRACE` macro:

| `SCOPED_TRACE(`_message_`);` |
|:-----------------------------|

where _message_ can be anything streamable to `std::ostream`. This
macro will cause the current file name, line number, and the given
message to be added in every failure message. The effect will be
undone when the control leaves the current lexical scope.

For example,

```
10: void Sub1(int n) {
11:   EXPECT_EQ(1, Bar(n));
12:   EXPECT_EQ(2, Bar(n + 1));
13: }
14:
15: TEST(FooTest, Bar) {
16:   {
17:     SCOPED_TRACE("A");  // This trace point will be included in
18:                         // every failure in this scope.
19:     Sub1(1);
20:   }
21:   // Now it won't.
22:   Sub1(9);
23: }
```

could result in messages like these:

```
path/to/foo_test.cc:11: Failure
Value of: Bar(n)
Expected: 1
  Actual: 2
   Trace:
path/to/foo_test.cc:17: A

path/to/foo_test.cc:12: Failure
Value of: Bar(n + 1)
Expected: 2
  Actual: 3
```

Without the trace, it would've been difficult to know which invocation
of `Sub1()` the two failures come from respectively. (You could add an
extra message to each assertion in `Sub1()` to indicate the value of
`n`, but that's tedious.)

Some tips on using `SCOPED_TRACE`:

  1. With a suitable message, it's often enough to use `SCOPED_TRACE` at the beginning of a sub-routine, instead of at each call site.
  1. When calling sub-routines inside a loop, make the loop iterator part of the message in `SCOPED_TRACE` such that you can know which iteration the failure is from.
  1. Sometimes the line number of the trace point is enough for identifying the particular invocation of a sub-routine. In this case, you don't have to choose a unique message for `SCOPED_TRACE`. You can simply use `""`.
  1. You can use `SCOPED_TRACE` in an inner scope when there is one in the outer scope. In this case, all active trace points will be included in the failure messages, in reverse order they are encountered.
  1. The trace dump is clickable in Emacs' compilation buffer - hit return on a line number and you'll be taken to that line in the source file!

_Availability:_ Linux, Windows, Mac.

## Propagating Fatal Failures ##

A common pitfall when using `ASSERT_*` and `FAIL*` is not understanding that
when they fail they only abort the _current function_, not the entire test. For
example, the following test will segfault:
```
void Subroutine() {
  // Generates a fatal failure and aborts the current function.
  ASSERT_EQ(1, 2);
  // The following won't be executed.
  ...
}

TEST(FooTest, Bar) {
  Subroutine();
  // The intended behavior is for the fatal failure
  // in Subroutine() to abort the entire test.
  // The actual behavior: the function goes on after Subroutine() returns.
  int* p = NULL;
  *p = 3; // Segfault!
}
```

Since we don't use exceptions, it is technically impossible to
implement the intended behavior here.  To alleviate this, Google Test
provides two solutions.  You could use either the
`(ASSERT|EXPECT)_NO_FATAL_FAILURE` assertions or the
`HasFatalFailure()` function.  They are described in the following two
subsections.

### Asserting on Subroutines ###

As shown above, if your test calls a subroutine that has an `ASSERT_*`
failure in it, the test will continue after the subroutine
returns. This may not be what you want.

Often people want fatal failures to propagate like exceptions.  For
that Google Test offers the following macros:

| **Fatal assertion** | **Nonfatal assertion** | **Verifies** |
|:---|:---|:---|
| `ASSERT_NO_FATAL_FAILURE(`_statement_`);` | `EXPECT_NO_FATAL_FAILURE(`_statement_`);` | _statement_ doesn't generate any new fatal failures in the current thread. |

Only failures in the thread that executes the assertion are checked to
determine the result of this type of assertions.  If _statement_
creates new threads, failures in these threads are ignored.

Examples:

```
ASSERT_NO_FATAL_FAILURE(Foo());

int i;
EXPECT_NO_FATAL_FAILURE({
  i = Bar();
});
```

_Availability:_ Linux, Windows, Mac. Assertions from multiple threads
are currently not supported.

### Checking for Failures in the Current Test ###

`HasFatalFailure()` in the `::testing::Test` class returns `true` if an
assertion in the current test has suffered a fatal failure. This
allows functions to catch fatal failures in a sub-routine and return
early.

```
class Test {
 public:
  ...
  static bool HasFatalFailure();
};
```

The typical usage, which basically simulates the behavior of a thrown
exception, is:

```
TEST(FooTest, Bar) {
  Subroutine();
  // Aborts if Subroutine() had a fatal failure.
  if (HasFatalFailure())
    return;
  // The following won't be executed.
  ...
}
```

If `HasFatalFailure()` is used outside of `TEST()` , `TEST_F()` , or a test
fixture, you must add the `::testing::Test::` prefix, as in:

```
if (::testing::Test::HasFatalFailure())
  return;
```

Similarly, `HasNonfatalFailure()` returns `true` if the current test
has at least one non-fatal failure, and `HasFailure()` returns `true`
if the current test has at least one failure of either kind.

_Availability:_ Linux, Windows, Mac.  `HasNonfatalFailure()` and
`HasFailure()` are available since version 1.4.0.

# Logging Additional Information #

In your test code, you can call `RecordProperty("key", value)` to log
additional information, where `value` can be either a string or an `int`. The _last_ value recorded for a key will be emitted to the XML output
if you specify one. For example, the test

```
TEST_F(WidgetUsageTest, MinAndMaxWidgets) {
  RecordProperty("MaximumWidgets", ComputeMaxUsage());
  RecordProperty("MinimumWidgets", ComputeMinUsage());
}
```

will output XML like this:

```
...
  <testcase name="MinAndMaxWidgets" status="run" time="6" classname="WidgetUsageTest"
            MaximumWidgets="12"
            MinimumWidgets="9" />
...
```

_Note_:
  * `RecordProperty()` is a static member of the `Test` class. Therefore it needs to be prefixed with `::testing::Test::` if used outside of the `TEST` body and the test fixture class.
  * `key` must be a valid XML attribute name, and cannot conflict with the ones already used by Google Test (`name`, `status`, `time`, `classname`, `type_param`, and `value_param`).
  * Calling `RecordProperty()` outside of the lifespan of a test is allowed. If it's called outside of a test but between a test case's `SetUpTestCase()` and `TearDownTestCase()` methods, it will be attributed to the XML element for the test case. If it's called outside of all test cases (e.g. in a test environment), it will be attributed to the top-level XML element.

_Availability_: Linux, Windows, Mac.

# Sharing Resources Between Tests in the Same Test Case #

Google Test creates a new test fixture object for each test in order to make
tests independent and easier to debug. However, sometimes tests use resources
that are expensive to set up, making the one-copy-per-test model prohibitively
expensive.

If the tests don't change the resource, there's no harm in them sharing a
single resource copy. So, in addition to per-test set-up/tear-down, Google Test
also supports per-test-case set-up/tear-down. To use it:

  1. In your test fixture class (say `FooTest` ), define as `static` some member variables to hold the shared resources.
  1. In the same test fixture class, define a `static void SetUpTestCase()` function (remember not to spell it as **`SetupTestCase`** with a small `u`!) to set up the shared resources and a `static void TearDownTestCase()` function to tear them down.

That's it! Google Test automatically calls `SetUpTestCase()` before running the
_first test_ in the `FooTest` test case (i.e. before creating the first
`FooTest` object), and calls `TearDownTestCase()` after running the _last test_
in it (i.e. after deleting the last `FooTest` object). In between, the tests
can use the shared resources.

Remember that the test order is undefined, so your code can't depend on a test
preceding or following another. Also, the tests must either not modify the
state of any shared resource, or, if they do modify the state, they must
restore the state to its original value before passing control to the next
test.

Here's an example of per-test-case set-up and tear-down:
```
class FooTest : public ::testing::Test {
 protected:
  // Per-test-case set-up.
  // Called before the first test in this test case.
  // Can be omitted if not needed.
  static void SetUpTestCase() {
    shared_resource_ = new ...;
  }

  // Per-test-case tear-down.
  // Called after the last test in this test case.
  // Can be omitted if not needed.
  static void TearDownTestCase() {
    delete shared_resource_;
    shared_resource_ = NULL;
  }

  // You can define per-test set-up and tear-down logic as usual.
  virtual void SetUp() { ... }
  virtual void TearDown() { ... }

  // Some expensive resource shared by all tests.
  static T* shared_resource_;
};

T* FooTest::shared_resource_ = NULL;

TEST_F(FooTest, Test1) {
  ... you can refer to shared_resource here ...
}
TEST_F(FooTest, Test2) {
  ... you can refer to shared_resource here ...
}
```

_Availability:_ Linux, Windows, Mac.

# Global Set-Up and Tear-Down #

Just as you can do set-up and tear-down at the test level and the test case
level, you can also do it at the test program level. Here's how.

First, you subclass the `::testing::Environment` class to define a test
environment, which knows how to set-up and tear-down:

```
class Environment {
 public:
  virtual ~Environment() {}
  // Override this to define how to set up the environment.
  virtual void SetUp() {}
  // Override this to define how to tear down the environment.
  virtual void TearDown() {}
};
```

Then, you register an instance of your environment class with Google Test by
calling the `::testing::AddGlobalTestEnvironment()` function:

```
Environment* AddGlobalTestEnvironment(Environment* env);
```

Now, when `RUN_ALL_TESTS()` is called, it first calls the `SetUp()` method of
the environment object, then runs the tests if there was no fatal failures, and
finally calls `TearDown()` of the environment object.

It's OK to register multiple environment objects. In this case, their `SetUp()`
will be called in the order they are registered, and their `TearDown()` will be
called in the reverse order.

Note that Google Test takes ownership of the registered environment objects.
Therefore **do not delete them** by yourself.

You should call `AddGlobalTestEnvironment()` before `RUN_ALL_TESTS()` is
called, probably in `main()`. If you use `gtest_main`, you need to      call
this before `main()` starts for it to take effect. One way to do this is to
define a global variable like this:

```
::testing::Environment* const foo_env = ::testing::AddGlobalTestEnvironment(new FooEnvironment);
```

However, we strongly recommend you to write your own `main()` and call
`AddGlobalTestEnvironment()` there, as relying on initialization of global
variables makes the code harder to read and may cause problems when you
register multiple environments from different translation units and the
environments have dependencies among them (remember that the compiler doesn't
guarantee the order in which global variables from different translation units
are initialized).

_Availability:_ Linux, Windows, Mac.

# Value Parameterized Tests #

_Value-parameterized tests_ allow you to test your code with different
parameters without writing multiple copies of the same test.

Suppose you write a test for your code and then realize that your code is affected by a presence of a Boolean command line flag.

```
TEST(MyCodeTest, TestFoo) {
  // A code to test foo().
}
```

Usually people factor their test code into a function with a Boolean parameter in such situations. The function sets the flag, then executes the testing code.

```
void TestFooHelper(bool flag_value) {
  flag = flag_value;
  // A code to test foo().
}

TEST(MyCodeTest, TestFoo) {
  TestFooHelper(false);
  TestFooHelper(true);
}
```

But this setup has serious drawbacks. First, when a test assertion fails in your tests, it becomes unclear what value of the parameter caused it to fail. You can stream a clarifying message into your `EXPECT`/`ASSERT` statements, but it you'll have to do it with all of them. Second, you have to add one such helper function per test. What if you have ten tests? Twenty? A hundred?

Value-parameterized tests will let you write your test only once and then easily instantiate and run it with an arbitrary number of parameter values.

Here are some other situations when value-parameterized tests come handy:

  * You want to test different implementations of an OO interface.
  * You want to test your code over various inputs (a.k.a. data-driven testing). This feature is easy to abuse, so please exercise your good sense when doing it!

## How to Write Value-Parameterized Tests ##

To write value-parameterized tests, first you should define a fixture
class.  It must be derived from both `::testing::Test` and
`::testing::WithParamInterface<T>` (the latter is a pure interface),
where `T` is the type of your parameter values.  For convenience, you
can just derive the fixture class from `::testing::TestWithParam<T>`,
which itself is derived from both `::testing::Test` and
`::testing::WithParamInterface<T>`. `T` can be any copyable type. If
it's a raw pointer, you are responsible for managing the lifespan of
the pointed values.

```
class FooTest : public ::testing::TestWithParam<const char*> {
  // You can implement all the usual fixture class members here.
  // To access the test parameter, call GetParam() from class
  // TestWithParam<T>.
};

// Or, when you want to add parameters to a pre-existing fixture class:
class BaseTest : public ::testing::Test {
  ...
};
class BarTest : public BaseTest,
                public ::testing::WithParamInterface<const char*> {
  ...
};
```

Then, use the `TEST_P` macro to define as many test patterns using
this fixture as you want.  The `_P` suffix is for "parameterized" or
"pattern", whichever you prefer to think.

```
TEST_P(FooTest, DoesBlah) {
  // Inside a test, access the test parameter with the GetParam() method
  // of the TestWithParam<T> class:
  EXPECT_TRUE(foo.Blah(GetParam()));
  ...
}

TEST_P(FooTest, HasBlahBlah) {
  ...
}
```

Finally, you can use `INSTANTIATE_TEST_CASE_P` to instantiate the test
case with any set of parameters you want. Google Test defines a number of
functions for generating test parameters. They return what we call
(surprise!) _parameter generators_. Here is a summary of them,
which are all in the `testing` namespace:

| `Range(begin, end[, step])` | Yields values `{begin, begin+step, begin+step+step, ...}`. The values do not include `end`. `step` defaults to 1. |
|:---|:---|
| `Values(v1, v2, ..., vN)` | Yields values `{v1, v2, ..., vN}`. |
| `ValuesIn(container)` and `ValuesIn(begin, end)` | Yields values from a C-style array, an STL-style container, or an iterator range `[begin, end)`. `container`, `begin`, and `end` can be expressions whose values are determined at run time.  |
| `Bool()` | Yields sequence `{false, true}`. |
| `Combine(g1, g2, ..., gN)`  | Yields all combinations (the Cartesian product for the math savvy) of the values generated by the `N` generators. This is only available if your system provides the `<tr1/tuple>` header. If you are sure your system does, and Google Test disagrees, you can override it by defining `GTEST_HAS_TR1_TUPLE=1`. See comments in [include/gtest/internal/gtest-port.h](../include/gtest/internal/gtest-port.h) for more information. |

For more details, see the comments at the definitions of these functions in the [source code](../include/gtest/gtest-param-test.h).

The following statement will instantiate tests from the `FooTest` test case
each with parameter values `"meeny"`, `"miny"`, and `"moe"`.

```
INSTANTIATE_TEST_CASE_P(InstantiationName,
                        FooTest,
                        ::testing::Values("meeny", "miny", "moe"));
```

To distinguish different instances of the pattern (yes, you can
instantiate it more than once), the first argument to
`INSTANTIATE_TEST_CASE_P` is a prefix that will be added to the actual
test case name. Remember to pick unique prefixes for different
instantiations. The tests from the instantiation above will have these
names:

  * `InstantiationName/FooTest.DoesBlah/0` for `"meeny"`
  * `InstantiationName/FooTest.DoesBlah/1` for `"miny"`
  * `InstantiationName/FooTest.DoesBlah/2` for `"moe"`
  * `InstantiationName/FooTest.HasBlahBlah/0` for `"meeny"`
  * `InstantiationName/FooTest.HasBlahBlah/1` for `"miny"`
  * `InstantiationName/FooTest.HasBlahBlah/2` for `"moe"`

You can use these names in [--gtest\_filter](#running-a-subset-of-the-tests).

This statement will instantiate all tests from `FooTest` again, each
with parameter values `"cat"` and `"dog"`:

```
const char* pets[] = {"cat", "dog"};
INSTANTIATE_TEST_CASE_P(AnotherInstantiationName, FooTest,
                        ::testing::ValuesIn(pets));
```

The tests from the instantiation above will have these names:

  * `AnotherInstantiationName/FooTest.DoesBlah/0` for `"cat"`
  * `AnotherInstantiationName/FooTest.DoesBlah/1` for `"dog"`
  * `AnotherInstantiationName/FooTest.HasBlahBlah/0` for `"cat"`
  * `AnotherInstantiationName/FooTest.HasBlahBlah/1` for `"dog"`

Please note that `INSTANTIATE_TEST_CASE_P` will instantiate _all_
tests in the given test case, whether their definitions come before or
_after_ the `INSTANTIATE_TEST_CASE_P` statement.

You can see
[these](../samples/sample7_unittest.cc)
[files](../samples/sample8_unittest.cc) for more examples.

_Availability_: Linux, Windows (requires MSVC 8.0 or above), Mac; since version 1.2.0.

## Creating Value-Parameterized Abstract Tests ##

In the above, we define and instantiate `FooTest` in the same source
file. Sometimes you may want to define value-parameterized tests in a
library and let other people instantiate them later. This pattern is
known as <i>abstract tests</i>. As an example of its application, when you
are designing an interface you can write a standard suite of abstract
tests (perhaps using a factory function as the test parameter) that
all implementations of the interface are expected to pass. When
someone implements the interface, he can instantiate your suite to get
all the interface-conformance tests for free.

To define abstract tests, you should organize your code like this:

  1. Put the definition of the parameterized test fixture class (e.g. `FooTest`) in a header file, say `foo_param_test.h`. Think of this as _declaring_ your abstract tests.
  1. Put the `TEST_P` definitions in `foo_param_test.cc`, which includes `foo_param_test.h`. Think of this as _implementing_ your abstract tests.

Once they are defined, you can instantiate them by including
`foo_param_test.h`, invoking `INSTANTIATE_TEST_CASE_P()`, and linking
with `foo_param_test.cc`. You can instantiate the same abstract test
case multiple times, possibly in different source files.

# Typed Tests #

Suppose you have multiple implementations of the same interface and
want to make sure that all of them satisfy some common requirements.
Or, you may have defined several types that are supposed to conform to
the same "concept" and you want to verify it.  In both cases, you want
the same test logic repeated for different types.

While you can write one `TEST` or `TEST_F` for each type you want to
test (and you may even factor the test logic into a function template
that you invoke from the `TEST`), it's tedious and doesn't scale:
if you want _m_ tests over _n_ types, you'll end up writing _m\*n_
`TEST`s.

_Typed tests_ allow you to repeat the same test logic over a list of
types.  You only need to write the test logic once, although you must
know the type list when writing typed tests.  Here's how you do it:

First, define a fixture class template.  It should be parameterized
by a type.  Remember to derive it from `::testing::Test`:

```
template <typename T>
class FooTest : public ::testing::Test {
 public:
  ...
  typedef std::list<T> List;
  static T shared_;
  T value_;
};
```

Next, associate a list of types with the test case, which will be
repeated for each type in the list:

```
typedef ::testing::Types<char, int, unsigned int> MyTypes;
TYPED_TEST_CASE(FooTest, MyTypes);
```

The `typedef` is necessary for the `TYPED_TEST_CASE` macro to parse
correctly.  Otherwise the compiler will think that each comma in the
type list introduces a new macro argument.

Then, use `TYPED_TEST()` instead of `TEST_F()` to define a typed test
for this test case.  You can repeat this as many times as you want:

```
TYPED_TEST(FooTest, DoesBlah) {
  // Inside a test, refer to the special name TypeParam to get the type
  // parameter.  Since we are inside a derived class template, C++ requires
  // us to visit the members of FooTest via 'this'.
  TypeParam n = this->value_;

  // To visit static members of the fixture, add the 'TestFixture::'
  // prefix.
  n += TestFixture::shared_;

  // To refer to typedefs in the fixture, add the 'typename TestFixture::'
  // prefix.  The 'typename' is required to satisfy the compiler.
  typename TestFixture::List values;
  values.push_back(n);
  ...
}

TYPED_TEST(FooTest, HasPropertyA) { ... }
```

You can see `samples/sample6_unittest.cc` for a complete example.

_Availability:_ Linux, Windows (requires MSVC 8.0 or above), Mac;
since version 1.1.0.

# Type-Parameterized Tests #

_Type-parameterized tests_ are like typed tests, except that they
don't require you to know the list of types ahead of time.  Instead,
you can define the test logic first and instantiate it with different
type lists later.  You can even instantiate it more than once in the
same program.

If you are designing an interface or concept, you can define a suite
of type-parameterized tests to verify properties that any valid
implementation of the interface/concept should have.  Then, the author
of each implementation can just instantiate the test suite with his
type to verify that it conforms to the requirements, without having to
write similar tests repeatedly.  Here's an example:

First, define a fixture class template, as we did with typed tests:

```
template <typename T>
class FooTest : public ::testing::Test {
  ...
};
```

Next, declare that you will define a type-parameterized test case:

```
TYPED_TEST_CASE_P(FooTest);
```

The `_P` suffix is for "parameterized" or "pattern", whichever you
prefer to think.

Then, use `TYPED_TEST_P()` to define a type-parameterized test.  You
can repeat this as many times as you want:

```
TYPED_TEST_P(FooTest, DoesBlah) {
  // Inside a test, refer to TypeParam to get the type parameter.
  TypeParam n = 0;
  ...
}

TYPED_TEST_P(FooTest, HasPropertyA) { ... }
```

Now the tricky part: you need to register all test patterns using the
`REGISTER_TYPED_TEST_CASE_P` macro before you can instantiate them.
The first argument of the macro is the test case name; the rest are
the names of the tests in this test case:

```
REGISTER_TYPED_TEST_CASE_P(FooTest,
                           DoesBlah, HasPropertyA);
```

Finally, you are free to instantiate the pattern with the types you
want.  If you put the above code in a header file, you can `#include`
it in multiple C++ source files and instantiate it multiple times.

```
typedef ::testing::Types<char, int, unsigned int> MyTypes;
INSTANTIATE_TYPED_TEST_CASE_P(My, FooTest, MyTypes);
```

To distinguish different instances of the pattern, the first argument
to the `INSTANTIATE_TYPED_TEST_CASE_P` macro is a prefix that will be
added to the actual test case name.  Remember to pick unique prefixes
for different instances.

In the special case where the type list contains only one type, you
can write that type directly without `::testing::Types<...>`, like this:

```
INSTANTIATE_TYPED_TEST_CASE_P(My, FooTest, int);
```

You can see `samples/sample6_unittest.cc` for a complete example.

_Availability:_ Linux, Windows (requires MSVC 8.0 or above), Mac;
since version 1.1.0.

# Testing Private Code #

If you change your software's internal implementation, your tests should not
break as long as the change is not observable by users. Therefore, per the
_black-box testing principle_, most of the time you should test your code
through its public interfaces.

If you still find yourself needing to test internal implementation code,
consider if there's a better design that wouldn't require you to do so. If you
absolutely have to test non-public interface code though, you can. There are
two cases to consider:

  * Static functions (_not_ the same as static member functions!) or unnamed namespaces, and
  * Private or protected class members

## Static Functions ##

Both static functions and definitions/declarations in an unnamed namespace are
only visible within the same translation unit. To test them, you can `#include`
the entire `.cc` file being tested in your `*_test.cc` file. (`#include`ing `.cc`
files is not a good way to reuse code - you should not do this in production
code!)

However, a better approach is to move the private code into the
`foo::internal` namespace, where `foo` is the namespace your project normally
uses, and put the private declarations in a `*-internal.h` file. Your
production `.cc` files and your tests are allowed to include this internal
header, but your clients are not. This way, you can fully test your internal
implementation without leaking it to your clients.

## Private Class Members ##

Private class members are only accessible from within the class or by friends.
To access a class' private members, you can declare your test fixture as a
friend to the class and define accessors in your fixture. Tests using the
fixture can then access the private members of your production class via the
accessors in the fixture. Note that even though your fixture is a friend to
your production class, your tests are not automatically friends to it, as they
are technically defined in sub-classes of the fixture.

Another way to test private members is to refactor them into an implementation
class, which is then declared in a `*-internal.h` file. Your clients aren't
allowed to include this header but your tests can. Such is called the Pimpl
(Private Implementation) idiom.

Or, you can declare an individual test as a friend of your class by adding this
line in the class body:

```
FRIEND_TEST(TestCaseName, TestName);
```

For example,
```
// foo.h
#include "gtest/gtest_prod.h"

// Defines FRIEND_TEST.
class Foo {
  ...
 private:
  FRIEND_TEST(FooTest, BarReturnsZeroOnNull);
  int Bar(void* x);
};

// foo_test.cc
...
TEST(FooTest, BarReturnsZeroOnNull) {
  Foo foo;
  EXPECT_EQ(0, foo.Bar(NULL));
  // Uses Foo's private member Bar().
}
```

Pay special attention when your class is defined in a namespace, as you should
define your test fixtures and tests in the same namespace if you want them to
be friends of your class. For example, if the code to be tested looks like:

```
namespace my_namespace {

class Foo {
  friend class FooTest;
  FRIEND_TEST(FooTest, Bar);
  FRIEND_TEST(FooTest, Baz);
  ...
  definition of the class Foo
  ...
};

}  // namespace my_namespace
```

Your test code should be something like:

```
namespace my_namespace {
class FooTest : public ::testing::Test {
 protected:
  ...
};

TEST_F(FooTest, Bar) { ... }
TEST_F(FooTest, Baz) { ... }

}  // namespace my_namespace
```

# Catching Failures #

If you are building a testing utility on top of Google Test, you'll
want to test your utility.  What framework would you use to test it?
Google Test, of course.

The challenge is to verify that your testing utility reports failures
correctly.  In frameworks that report a failure by throwing an
exception, you could catch the exception and assert on it.  But Google
Test doesn't use exceptions, so how do we test that a piece of code
generates an expected failure?

`"gtest/gtest-spi.h"` contains some constructs to do this.  After 
`#include`ing this header, you can use

| `EXPECT_FATAL_FAILURE(`_statement, substring_`);` |
|:--------------------------------------------------|

to assert that _statement_ generates a fatal (e.g. `ASSERT_*`) failure
whose message contains the given _substring_, or use

| `EXPECT_NONFATAL_FAILURE(`_statement, substring_`);` |
|:-----------------------------------------------------|

if you are expecting a non-fatal (e.g. `EXPECT_*`) failure.

For technical reasons, there are some caveats:

  1. You cannot stream a failure message to either macro.
  1. _statement_ in `EXPECT_FATAL_FAILURE()` cannot reference local non-static variables or non-static members of `this` object.
  1. _statement_ in `EXPECT_FATAL_FAILURE()` cannot return a value.

_Note:_ Google Test is designed with threads in mind. Once the
synchronization primitives in `"gtest/internal/gtest-port.h"` have
been implemented, Google Test will become thread-safe, meaning that
you can then use assertions in multiple threads concurrently. Before
that, however, Google Test only supports single-threaded usage. Once
thread-safe, `EXPECT_FATAL_FAILURE()` and `EXPECT_NONFATAL_FAILURE()`
will capture failures in the current thread only. If _statement_
creates new threads, failures in these threads will be ignored. If
you want to capture failures from all threads instead, you should use
the following macros:

| `EXPECT_FATAL_FAILURE_ON_ALL_THREADS(`_statement, substring_`);` |
|:-----------------------------------------------------------------|
| `EXPECT_NONFATAL_FAILURE_ON_ALL_THREADS(`_statement, substring_`);` |

# Getting the Current Test's Name #

Sometimes a function may need to know the name of the currently running test.
For example, you may be using the `SetUp()` method of your test fixture to set
the golden file name based on which test is running. The `::testing::TestInfo`
class has this information:

```
namespace testing {

class TestInfo {
 public:
  // Returns the test case name and the test name, respectively.
  //
  // Do NOT delete or free the return value - it's managed by the
  // TestInfo class.
  const char* test_case_name() const;
  const char* name() const;
};

}  // namespace testing
```

> To obtain a `TestInfo` object for the currently running test, call
`current_test_info()` on the `UnitTest` singleton object:

```
// Gets information about the currently running test.
// Do NOT delete the returned object - it's managed by the UnitTest class.
const ::testing::TestInfo* const test_info =
  ::testing::UnitTest::GetInstance()->current_test_info();
printf("We are in test %s of test case %s.\n",
       test_info->name(), test_info->test_case_name());
```

`current_test_info()` returns a null pointer if no test is running. In
particular, you cannot find the test case name in `TestCaseSetUp()`,
`TestCaseTearDown()` (where you know the test case name implicitly), or
functions called from them.

_Availability:_ Linux, Windows, Mac.

# Extending Google Test by Handling Test Events #

Google Test provides an <b>event listener API</b> to let you receive
notifications about the progress of a test program and test
failures. The events you can listen to include the start and end of
the test program, a test case, or a test method, among others. You may
use this API to augment or replace the standard console output,
replace the XML output, or provide a completely different form of
output, such as a GUI or a database. You can also use test events as
checkpoints to implement a resource leak checker, for example.

_Availability:_ Linux, Windows, Mac; since v1.4.0.

## Defining Event Listeners ##

To define a event listener, you subclass either
[testing::TestEventListener](../include/gtest/gtest.h#L991)
or [testing::EmptyTestEventListener](../include/gtest/gtest.h#L1044).
The former is an (abstract) interface, where <i>each pure virtual method<br>
can be overridden to handle a test event</i> (For example, when a test
starts, the `OnTestStart()` method will be called.). The latter provides
an empty implementation of all methods in the interface, such that a
subclass only needs to override the methods it cares about.

When an event is fired, its context is passed to the handler function
as an argument. The following argument types are used:
  * [UnitTest](../include/gtest/gtest.h#L1151) reflects the state of the entire test program,
  * [TestCase](../include/gtest/gtest.h#L778) has information about a test case, which can contain one or more tests,
  * [TestInfo](../include/gtest/gtest.h#L644) contains the state of a test, and
  * [TestPartResult](../include/gtest/gtest-test-part.h#L47) represents the result of a test assertion.

An event handler function can examine the argument it receives to find
out interesting information about the event and the test program's
state.  Here's an example:

```
  class MinimalistPrinter : public ::testing::EmptyTestEventListener {
    // Called before a test starts.
    virtual void OnTestStart(const ::testing::TestInfo& test_info) {
      printf("*** Test %s.%s starting.\n",
             test_info.test_case_name(), test_info.name());
    }

    // Called after a failed assertion or a SUCCEED() invocation.
    virtual void OnTestPartResult(
        const ::testing::TestPartResult& test_part_result) {
      printf("%s in %s:%d\n%s\n",
             test_part_result.failed() ? "*** Failure" : "Success",
             test_part_result.file_name(),
             test_part_result.line_number(),
             test_part_result.summary());
    }

    // Called after a test ends.
    virtual void OnTestEnd(const ::testing::TestInfo& test_info) {
      printf("*** Test %s.%s ending.\n",
             test_info.test_case_name(), test_info.name());
    }
  };
```

## Using Event Listeners ##

To use the event listener you have defined, add an instance of it to
the Google Test event listener list (represented by class
[TestEventListeners](../include/gtest/gtest.h#L1064)
- note the "s" at the end of the name) in your
`main()` function, before calling `RUN_ALL_TESTS()`:
```
int main(int argc, char** argv) {
  ::testing::InitGoogleTest(&argc, argv);
  // Gets hold of the event listener list.
  ::testing::TestEventListeners& listeners =
      ::testing::UnitTest::GetInstance()->listeners();
  // Adds a listener to the end.  Google Test takes the ownership.
  listeners.Append(new MinimalistPrinter);
  return RUN_ALL_TESTS();
}
```

There's only one problem: the default test result printer is still in
effect, so its output will mingle with the output from your minimalist
printer. To suppress the default printer, just release it from the
event listener list and delete it. You can do so by adding one line:
```
  ...
  delete listeners.Release(listeners.default_result_printer());
  listeners.Append(new MinimalistPrinter);
  return RUN_ALL_TESTS();
```

Now, sit back and enjoy a completely different output from your
tests. For more details, you can read this
[sample](../samples/sample9_unittest.cc).

You may append more than one listener to the list. When an `On*Start()`
or `OnTestPartResult()` event is fired, the listeners will receive it in
the order they appear in the list (since new listeners are added to
the end of the list, the default text printer and the default XML
generator will receive the event first). An `On*End()` event will be
received by the listeners in the _reverse_ order. This allows output by
listeners added later to be framed by output from listeners added
earlier.

## Generating Failures in Listeners ##

You may use failure-raising macros (`EXPECT_*()`, `ASSERT_*()`,
`FAIL()`, etc) when processing an event. There are some restrictions:

  1. You cannot generate any failure in `OnTestPartResult()` (otherwise it will cause `OnTestPartResult()` to be called recursively).
  1. A listener that handles `OnTestPartResult()` is not allowed to generate any failure.

When you add listeners to the listener list, you should put listeners
that handle `OnTestPartResult()` _before_ listeners that can generate
failures. This ensures that failures generated by the latter are
attributed to the right test by the former.

We have a sample of failure-raising listener
[here](../samples/sample10_unittest.cc).

# Running Test Programs: Advanced Options #

Google Test test programs are ordinary executables. Once built, you can run
them directly and affect their behavior via the following environment variables
and/or command line flags. For the flags to work, your programs must call
`::testing::InitGoogleTest()` before calling `RUN_ALL_TESTS()`.

To see a list of supported flags and their usage, please run your test
program with the `--help` flag.  You can also use `-h`, `-?`, or `/?`
for short.  This feature is added in version 1.3.0.

If an option is specified both by an environment variable and by a
flag, the latter takes precedence.  Most of the options can also be
set/read in code: to access the value of command line flag
`--gtest_foo`, write `::testing::GTEST_FLAG(foo)`.  A common pattern is
to set the value of a flag before calling `::testing::InitGoogleTest()`
to change the default value of the flag:
```
int main(int argc, char** argv) {
  // Disables elapsed time by default.
  ::testing::GTEST_FLAG(print_time) = false;

  // This allows the user to override the flag on the command line.
  ::testing::InitGoogleTest(&argc, argv);

  return RUN_ALL_TESTS();
}
```

## Selecting Tests ##

This section shows various options for choosing which tests to run.

### Listing Test Names ###

Sometimes it is necessary to list the available tests in a program before
running them so that a filter may be applied if needed. Including the flag
`--gtest_list_tests` overrides all other flags and lists tests in the following
format:
```
TestCase1.
  TestName1
  TestName2
TestCase2.
  TestName
```

None of the tests listed are actually run if the flag is provided. There is no
corresponding environment variable for this flag.

_Availability:_ Linux, Windows, Mac.

### Running a Subset of the Tests ###

By default, a Google Test program runs all tests the user has defined.
Sometimes, you want to run only a subset of the tests (e.g. for debugging or
quickly verifying a change). If you set the `GTEST_FILTER` environment variable
or the `--gtest_filter` flag to a filter string, Google Test will only run the
tests whose full names (in the form of `TestCaseName.TestName`) match the
filter.

The format of a filter is a '`:`'-separated list of wildcard patterns (called
the positive patterns) optionally followed by a '`-`' and another
'`:`'-separated pattern list (called the negative patterns). A test matches the
filter if and only if it matches any of the positive patterns but does not
match any of the negative patterns.

A pattern may contain `'*'` (matches any string) or `'?'` (matches any single
character). For convenience, the filter `'*-NegativePatterns'` can be also
written as `'-NegativePatterns'`.

For example:

  * `./foo_test` Has no flag, and thus runs all its tests.
  * `./foo_test --gtest_filter=*` Also runs everything, due to the single match-everything `*` value.
  * `./foo_test --gtest_filter=FooTest.*` Runs everything in test case `FooTest`.
  * `./foo_test --gtest_filter=*Null*:*Constructor*` Runs any test whose full name contains either `"Null"` or `"Constructor"`.
  * `./foo_test --gtest_filter=-*DeathTest.*` Runs all non-death tests.
  * `./foo_test --gtest_filter=FooTest.*-FooTest.Bar` Runs everything in test case `FooTest` except `FooTest.Bar`.

_Availability:_ Linux, Windows, Mac.

### Temporarily Disabling Tests ###

If you have a broken test that you cannot fix right away, you can add the
`DISABLED_` prefix to its name. This will exclude it from execution. This is
better than commenting out the code or using `#if 0`, as disabled tests are
still compiled (and thus won't rot).

If you need to disable all tests in a test case, you can either add `DISABLED_`
to the front of the name of each test, or alternatively add it to the front of
the test case name.

For example, the following tests won't be run by Google Test, even though they
will still be compiled:

```
// Tests that Foo does Abc.
TEST(FooTest, DISABLED_DoesAbc) { ... }

class DISABLED_BarTest : public ::testing::Test { ... };

// Tests that Bar does Xyz.
TEST_F(DISABLED_BarTest, DoesXyz) { ... }
```

_Note:_ This feature should only be used for temporary pain-relief. You still
have to fix the disabled tests at a later date. As a reminder, Google Test will
print a banner warning you if a test program contains any disabled tests.

_Tip:_ You can easily count the number of disabled tests you have
using `grep`. This number can be used as a metric for improving your
test quality.

_Availability:_ Linux, Windows, Mac.

### Temporarily Enabling Disabled Tests ###

To include [disabled tests](#temporarily-disabling-tests) in test
execution, just invoke the test program with the
`--gtest_also_run_disabled_tests` flag or set the
`GTEST_ALSO_RUN_DISABLED_TESTS` environment variable to a value other
than `0`.  You can combine this with the
[--gtest\_filter](#running-a-subset-of-the-tests) flag to further select
which disabled tests to run.

_Availability:_ Linux, Windows, Mac; since version 1.3.0.

## Repeating the Tests ##

Once in a while you'll run into a test whose result is hit-or-miss. Perhaps it
will fail only 1% of the time, making it rather hard to reproduce the bug under
a debugger. This can be a major source of frustration.

The `--gtest_repeat` flag allows you to repeat all (or selected) test methods
in a program many times. Hopefully, a flaky test will eventually fail and give
you a chance to debug. Here's how to use it:

| `$ foo_test --gtest_repeat=1000` | Repeat foo\_test 1000 times and don't stop at failures. |
|:---|:---|
| `$ foo_test --gtest_repeat=-1` | A negative count means repeating forever. |
| `$ foo_test --gtest_repeat=1000 --gtest_break_on_failure` | Repeat foo\_test 1000 times, stopping at the first failure. This is especially useful when running under a debugger: when the testfails, it will drop into the debugger and you can then inspect variables and stacks. |
| `$ foo_test --gtest_repeat=1000 --gtest_filter=FooBar` | Repeat the tests whose name matches the filter 1000 times. |

If your test program contains global set-up/tear-down code registered
using `AddGlobalTestEnvironment()`, it will be repeated in each
iteration as well, as the flakiness may be in it. You can also specify
the repeat count by setting the `GTEST_REPEAT` environment variable.

_Availability:_ Linux, Windows, Mac.

## Shuffling the Tests ##

You can specify the `--gtest_shuffle` flag (or set the `GTEST_SHUFFLE`
environment variable to `1`) to run the tests in a program in a random
order. This helps to reveal bad dependencies between tests.

By default, Google Test uses a random seed calculated from the current
time. Therefore you'll get a different order every time. The console
output includes the random seed value, such that you can reproduce an
order-related test failure later. To specify the random seed
explicitly, use the `--gtest_random_seed=SEED` flag (or set the
`GTEST_RANDOM_SEED` environment variable), where `SEED` is an integer
between 0 and 99999. The seed value 0 is special: it tells Google Test
to do the default behavior of calculating the seed from the current
time.

If you combine this with `--gtest_repeat=N`, Google Test will pick a
different random seed and re-shuffle the tests in each iteration.

_Availability:_ Linux, Windows, Mac; since v1.4.0.

## Controlling Test Output ##

This section teaches how to tweak the way test results are reported.

### Colored Terminal Output ###

Google Test can use colors in its terminal output to make it easier to spot
the separation between tests, and whether tests passed.

You can set the GTEST\_COLOR environment variable or set the `--gtest_color`
command line flag to `yes`, `no`, or `auto` (the default) to enable colors,
disable colors, or let Google Test decide. When the value is `auto`, Google
Test will use colors if and only if the output goes to a terminal and (on
non-Windows platforms) the `TERM` environment variable is set to `xterm` or
`xterm-color`.

_Availability:_ Linux, Windows, Mac.

### Suppressing the Elapsed Time ###

By default, Google Test prints the time it takes to run each test.  To
suppress that, run the test program with the `--gtest_print_time=0`
command line flag.  Setting the `GTEST_PRINT_TIME` environment
variable to `0` has the same effect.

_Availability:_ Linux, Windows, Mac.  (In Google Test 1.3.0 and lower,
the default behavior is that the elapsed time is **not** printed.)

### Generating an XML Report ###

Google Test can emit a detailed XML report to a file in addition to its normal
textual output. The report contains the duration of each test, and thus can
help you identify slow tests.

To generate the XML report, set the `GTEST_OUTPUT` environment variable or the
`--gtest_output` flag to the string `"xml:_path_to_output_file_"`, which will
create the file at the given location. You can also just use the string
`"xml"`, in which case the output can be found in the `test_detail.xml` file in
the current directory.

If you specify a directory (for example, `"xml:output/directory/"` on Linux or
`"xml:output\directory\"` on Windows), Google Test will create the XML file in
that directory, named after the test executable (e.g. `foo_test.xml` for test
program `foo_test` or `foo_test.exe`). If the file already exists (perhaps left
over from a previous run), Google Test will pick a different name (e.g.
`foo_test_1.xml`) to avoid overwriting it.

The report uses the format described here.  It is based on the
`junitreport` Ant task and can be parsed by popular continuous build
systems like [Hudson](https://hudson.dev.java.net/). Since that format
was originally intended for Java, a little interpretation is required
to make it apply to Google Test tests, as shown here:

```
<testsuites name="AllTests" ...>
  <testsuite name="test_case_name" ...>
    <testcase name="test_name" ...>
      <failure message="..."/>
      <failure message="..."/>
      <failure message="..."/>
    </testcase>
  </testsuite>
</testsuites>
```

  * The root `<testsuites>` element corresponds to the entire test program.
  * `<testsuite>` elements correspond to Google Test test cases.
  * `<testcase>` elements correspond to Google Test test functions.

For instance, the following program

```
TEST(MathTest, Addition) { ... }
TEST(MathTest, Subtraction) { ... }
TEST(LogicTest, NonContradiction) { ... }
```

could generate this report:

```
<?xml version="1.0" encoding="UTF-8"?>
<testsuites tests="3" failures="1" errors="0" time="35" name="AllTests">
  <testsuite name="MathTest" tests="2" failures="1" errors="0" time="15">
    <testcase name="Addition" status="run" time="7" classname="">
      <failure message="Value of: add(1, 1)&#x0A; Actual: 3&#x0A;Expected: 2" type=""/>
      <failure message="Value of: add(1, -1)&#x0A; Actual: 1&#x0A;Expected: 0" type=""/>
    </testcase>
    <testcase name="Subtraction" status="run" time="5" classname="">
    </testcase>
  </testsuite>
  <testsuite name="LogicTest" tests="1" failures="0" errors="0" time="5">
    <testcase name="NonContradiction" status="run" time="5" classname="">
    </testcase>
  </testsuite>
</testsuites>
```

Things to note:

  * The `tests` attribute of a `<testsuites>` or `<testsuite>` element tells how many test functions the Google Test program or test case contains, while the `failures` attribute tells how many of them failed.
  * The `time` attribute expresses the duration of the test, test case, or entire test program in milliseconds.
  * Each `<failure>` element corresponds to a single failed Google Test assertion.
  * Some JUnit concepts don't apply to Google Test, yet we have to conform to the DTD. Therefore you'll see some dummy elements and attributes in the report. You can safely ignore these parts.

_Availability:_ Linux, Windows, Mac.

## Controlling How Failures Are Reported ##

### Turning Assertion Failures into Break-Points ###

When running test programs under a debugger, it's very convenient if the
debugger can catch an assertion failure and automatically drop into interactive
mode. Google Test's _break-on-failure_ mode supports this behavior.

To enable it, set the `GTEST_BREAK_ON_FAILURE` environment variable to a value
other than `0` . Alternatively, you can use the `--gtest_break_on_failure`
command line flag.

_Availability:_ Linux, Windows, Mac.

### Disabling Catching Test-Thrown Exceptions ###

Google Test can be used either with or without exceptions enabled.  If
a test throws a C++ exception or (on Windows) a structured exception
(SEH), by default Google Test catches it, reports it as a test
failure, and continues with the next test method.  This maximizes the
coverage of a test run.  Also, on Windows an uncaught exception will
cause a pop-up window, so catching the exceptions allows you to run
the tests automatically.

When debugging the test failures, however, you may instead want the
exceptions to be handled by the debugger, such that you can examine
the call stack when an exception is thrown.  To achieve that, set the
`GTEST_CATCH_EXCEPTIONS` environment variable to `0`, or use the
`--gtest_catch_exceptions=0` flag when running the tests.

**Availability**: Linux, Windows, Mac.

### Letting Another Testing Framework Drive ###

If you work on a project that has already been using another testing
framework and is not ready to completely switch to Google Test yet,
you can get much of Google Test's benefit by using its assertions in
your existing tests.  Just change your `main()` function to look
like:

```
#include "gtest/gtest.h"

int main(int argc, char** argv) {
  ::testing::GTEST_FLAG(throw_on_failure) = true;
  // Important: Google Test must be initialized.
  ::testing::InitGoogleTest(&argc, argv);

  ... whatever your existing testing framework requires ...
}
```

With that, you can use Google Test assertions in addition to the
native assertions your testing framework provides, for example:

```
void TestFooDoesBar() {
  Foo foo;
  EXPECT_LE(foo.Bar(1), 100);     // A Google Test assertion.
  CPPUNIT_ASSERT(foo.IsEmpty());  // A native assertion.
}
```

If a Google Test assertion fails, it will print an error message and
throw an exception, which will be treated as a failure by your host
testing framework.  If you compile your code with exceptions disabled,
a failed Google Test assertion will instead exit your program with a
non-zero code, which will also signal a test failure to your test
runner.

If you don't write `::testing::GTEST_FLAG(throw_on_failure) = true;` in
your `main()`, you can alternatively enable this feature by specifying
the `--gtest_throw_on_failure` flag on the command-line or setting the
`GTEST_THROW_ON_FAILURE` environment variable to a non-zero value.

Death tests are _not_ supported when other test framework is used to organize tests.

_Availability:_ Linux, Windows, Mac; since v1.3.0.

## Distributing Test Functions to Multiple Machines ##

If you have more than one machine you can use to run a test program,
you might want to run the test functions in parallel and get the
result faster.  We call this technique _sharding_, where each machine
is called a _shard_.

Google Test is compatible with test sharding.  To take advantage of
this feature, your test runner (not part of Google Test) needs to do
the following:

  1. Allocate a number of machines (shards) to run the tests.
  1. On each shard, set the `GTEST_TOTAL_SHARDS` environment variable to the total number of shards.  It must be the same for all shards.
  1. On each shard, set the `GTEST_SHARD_INDEX` environment variable to the index of the shard.  Different shards must be assigned different indices, which must be in the range `[0, GTEST_TOTAL_SHARDS - 1]`.
  1. Run the same test program on all shards.  When Google Test sees the above two environment variables, it will select a subset of the test functions to run.  Across all shards, each test function in the program will be run exactly once.
  1. Wait for all shards to finish, then collect and report the results.

Your project may have tests that were written without Google Test and
thus don't understand this protocol.  In order for your test runner to
figure out which test supports sharding, it can set the environment
variable `GTEST_SHARD_STATUS_FILE` to a non-existent file path.  If a
test program supports sharding, it will create this file to
acknowledge the fact (the actual contents of the file are not
important at this time; although we may stick some useful information
in it in the future.); otherwise it will not create it.

Here's an example to make it clear.  Suppose you have a test program
`foo_test` that contains the following 5 test functions:
```
TEST(A, V)
TEST(A, W)
TEST(B, X)
TEST(B, Y)
TEST(B, Z)
```
and you have 3 machines at your disposal.  To run the test functions in
parallel, you would set `GTEST_TOTAL_SHARDS` to 3 on all machines, and
set `GTEST_SHARD_INDEX` to 0, 1, and 2 on the machines respectively.
Then you would run the same `foo_test` on each machine.

Google Test reserves the right to change how the work is distributed
across the shards, but here's one possible scenario:

  * Machine #0 runs `A.V` and `B.X`.
  * Machine #1 runs `A.W` and `B.Y`.
  * Machine #2 runs `B.Z`.

_Availability:_ Linux, Windows, Mac; since version 1.3.0.

# Fusing Google Test Source Files #

Google Test's implementation consists of ~30 files (excluding its own
tests).  Sometimes you may want them to be packaged up in two files (a
`.h` and a `.cc`) instead, such that you can easily copy them to a new
machine and start hacking there.  For this we provide an experimental
Python script `fuse_gtest_files.py` in the `scripts/` directory (since release 1.3.0).
Assuming you have Python 2.4 or above installed on your machine, just
go to that directory and run
```
python fuse_gtest_files.py OUTPUT_DIR
```

and you should see an `OUTPUT_DIR` directory being created with files
`gtest/gtest.h` and `gtest/gtest-all.cc` in it.  These files contain
everything you need to use Google Test.  Just copy them to anywhere
you want and you are ready to write tests.  You can use the
[scripts/test/Makefile](../scripts/test/Makefile)
file as an example on how to compile your tests against them.

# Where to Go from Here #

Congratulations! You've now learned more advanced Google Test tools and are
ready to tackle more complex testing tasks. If you want to dive even deeper, you
can read the [Frequently-Asked Questions](FAQ.md).

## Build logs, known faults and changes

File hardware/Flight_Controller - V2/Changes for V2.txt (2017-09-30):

Changes for V2:

Tent all vias (or at least ones under chips and ones that could easily short
rgb leds?
more test points
pullup on reset button
maybe larger holes for connector
longer pads on lga chips
I2C vs SPI?
SPI broken out for SD Card logging
reverse polarity protection

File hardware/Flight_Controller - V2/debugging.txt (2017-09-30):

led1 shorted to led2, might be between viass under micro

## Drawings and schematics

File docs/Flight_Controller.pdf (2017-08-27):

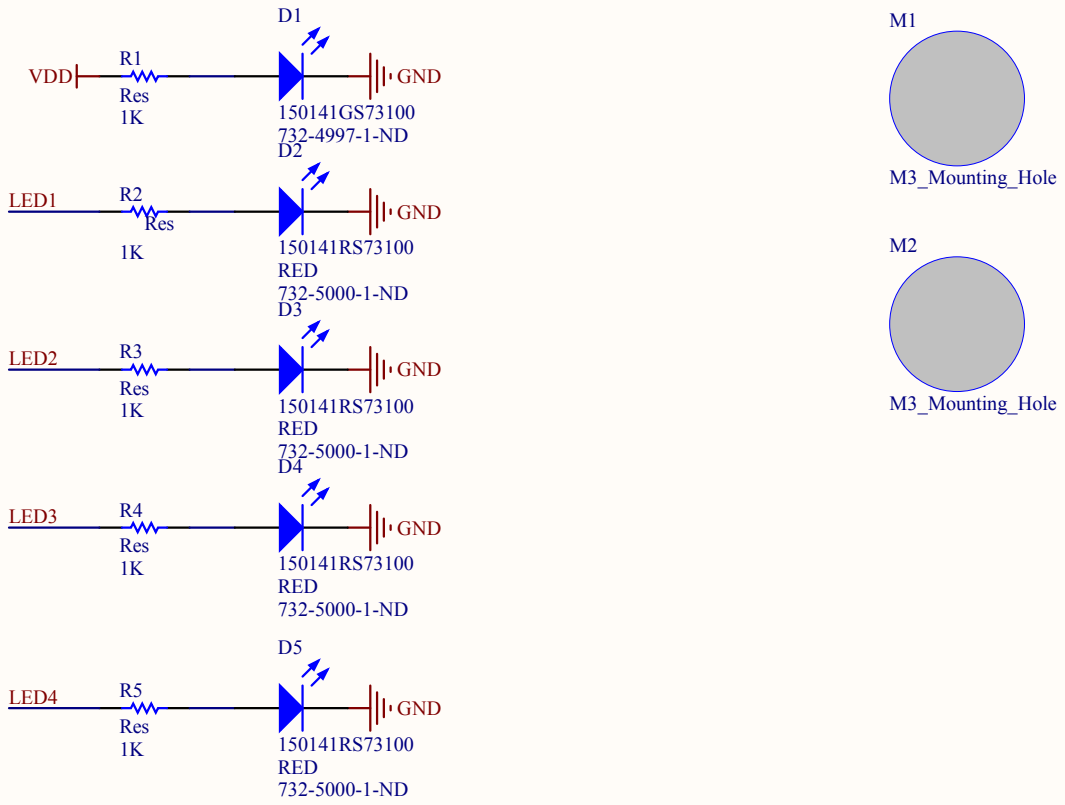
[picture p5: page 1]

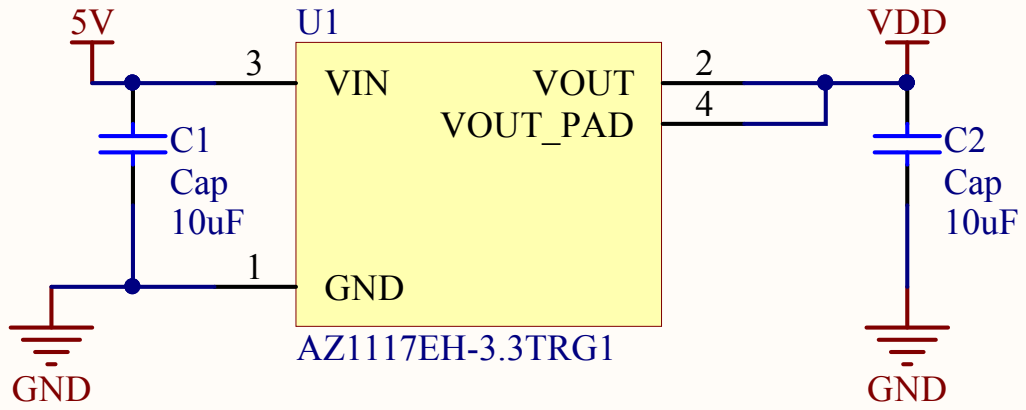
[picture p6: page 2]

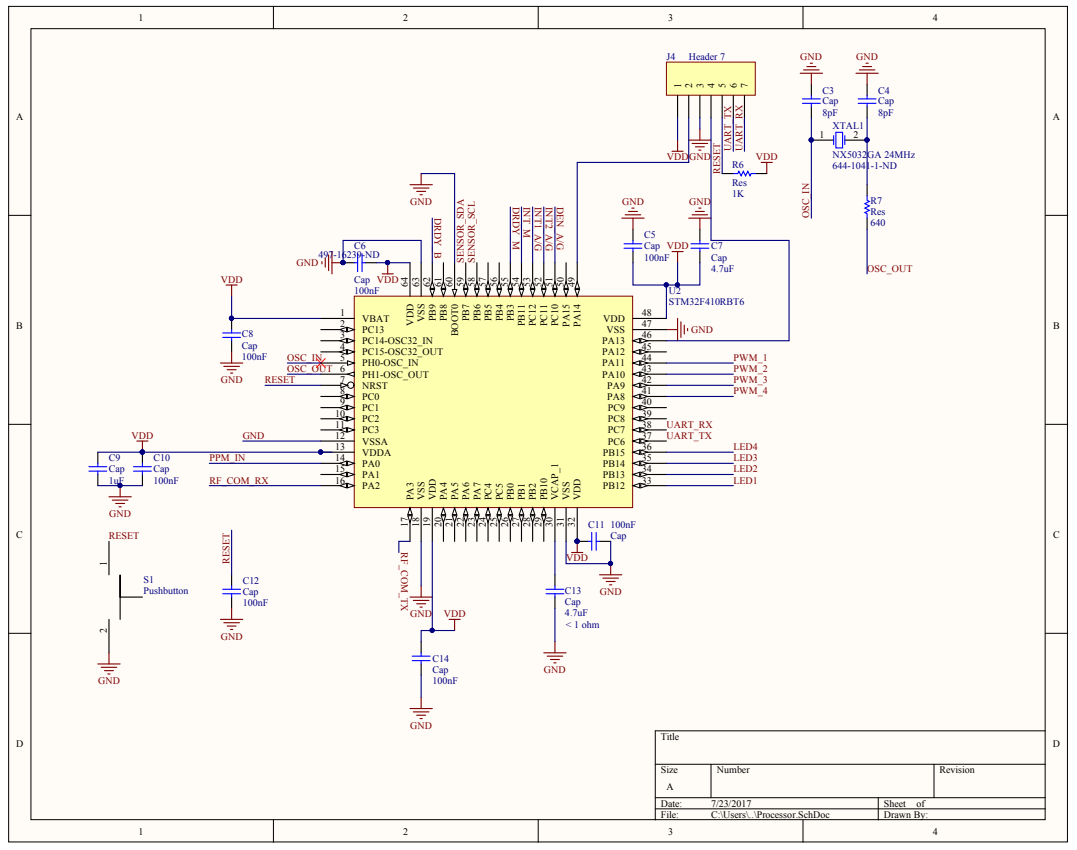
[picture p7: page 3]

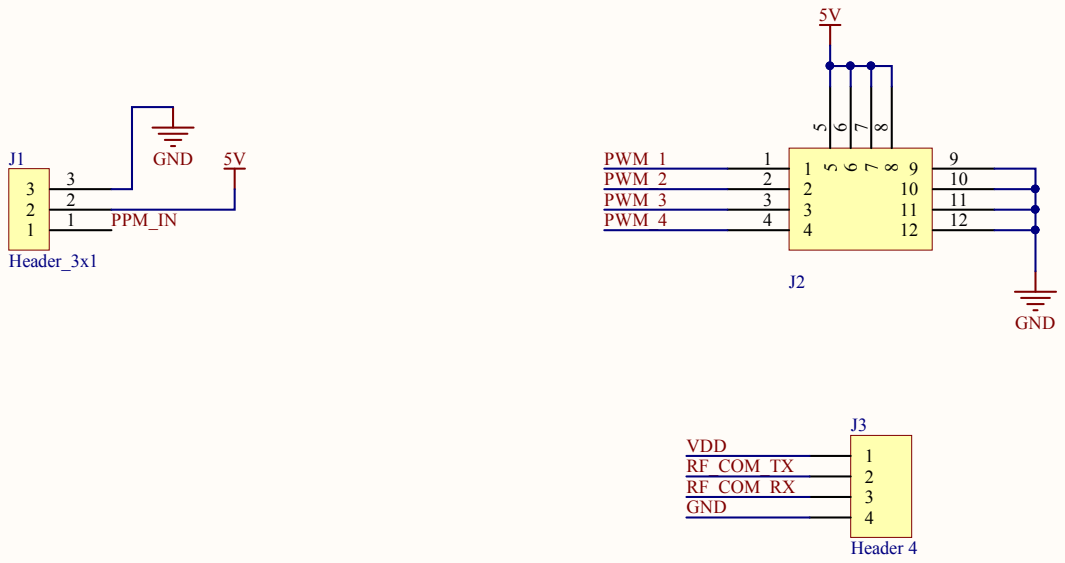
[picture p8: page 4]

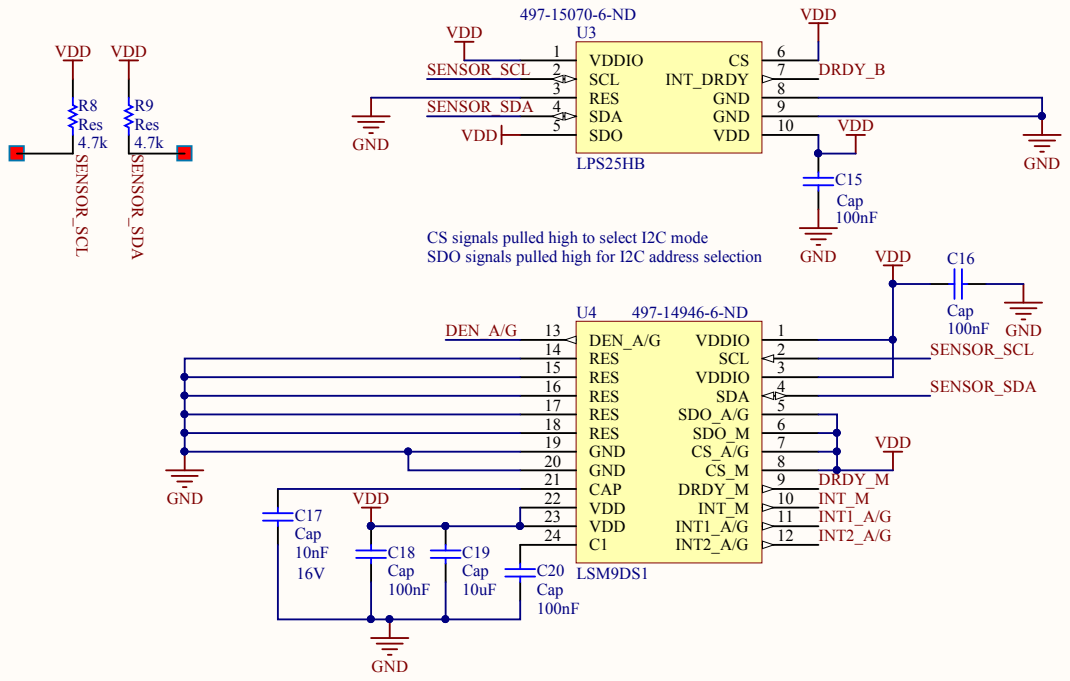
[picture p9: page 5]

CS signals pulled high to select I2C mode
SDO signals pulled high for I2C address selection

VDD 22 VDD 23

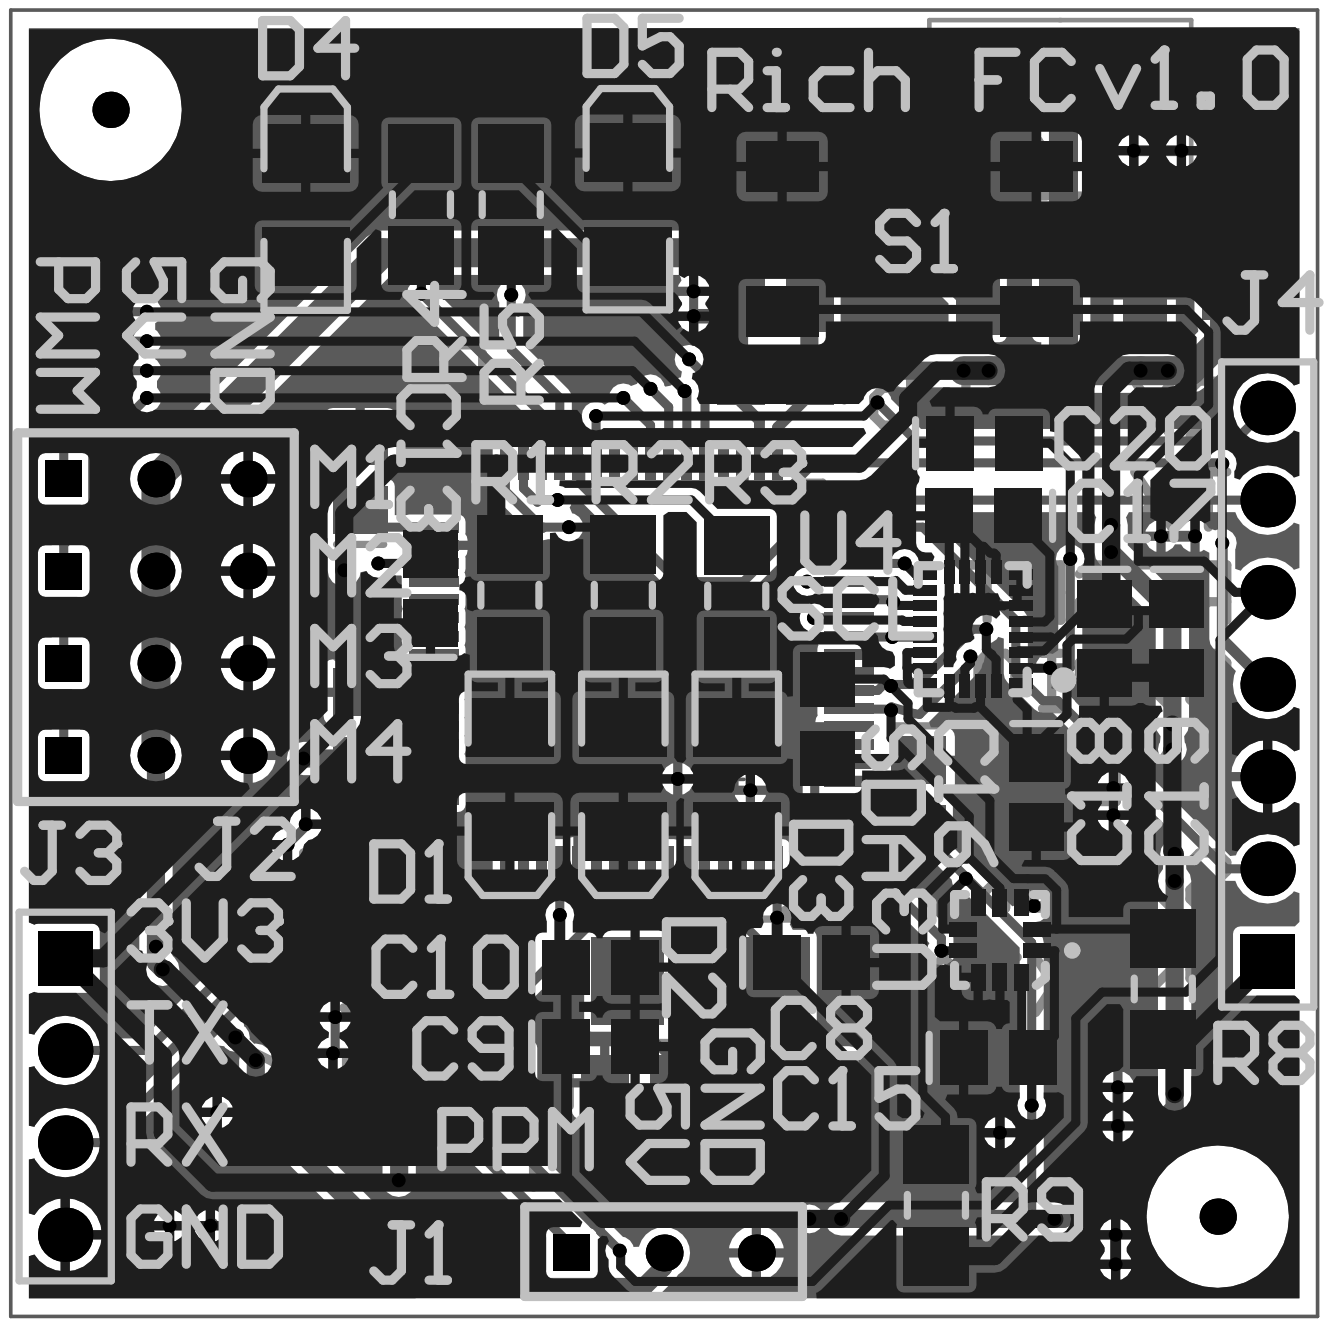
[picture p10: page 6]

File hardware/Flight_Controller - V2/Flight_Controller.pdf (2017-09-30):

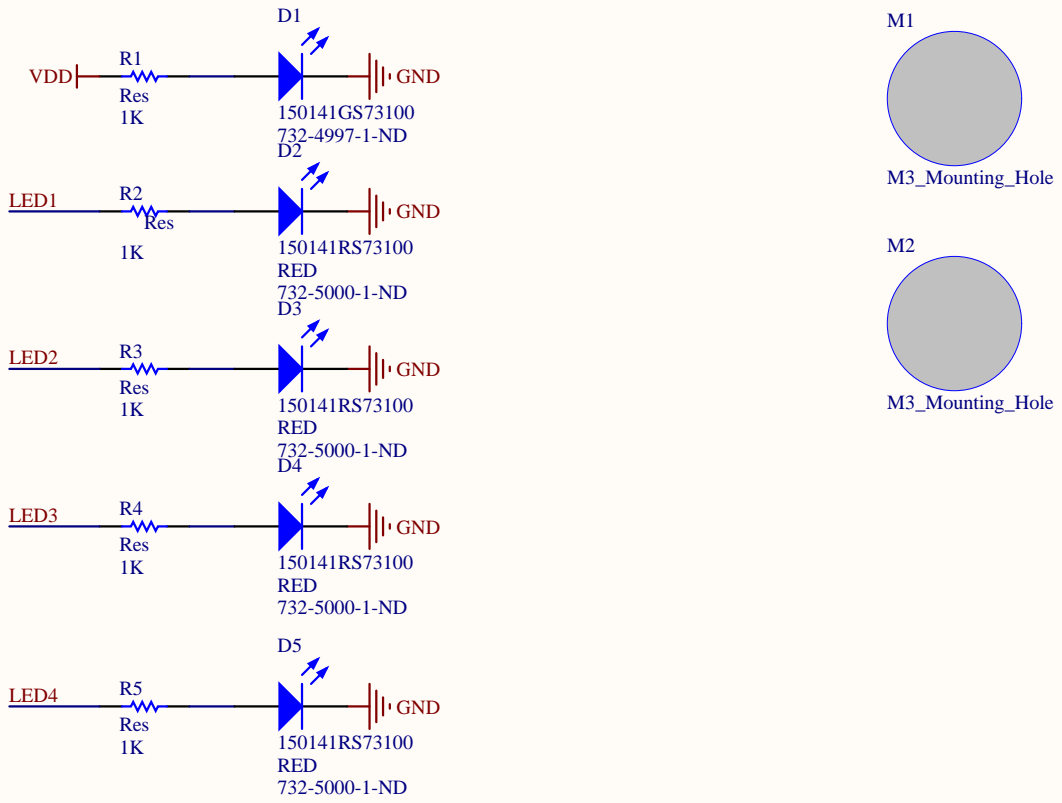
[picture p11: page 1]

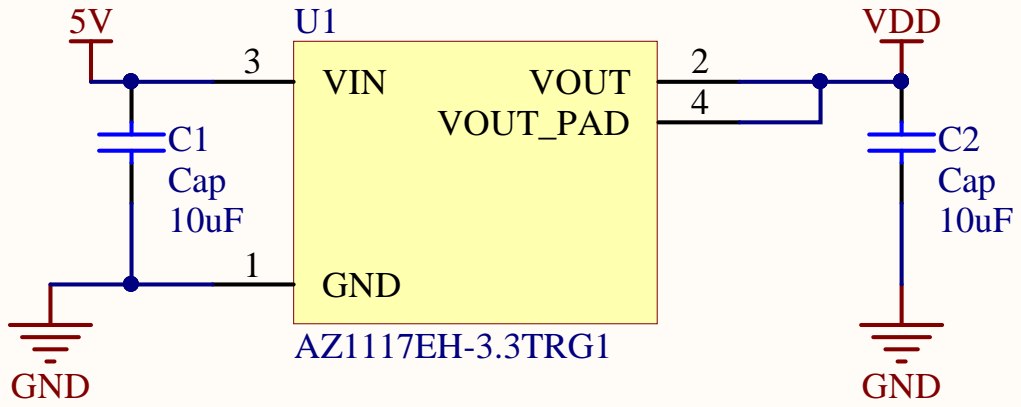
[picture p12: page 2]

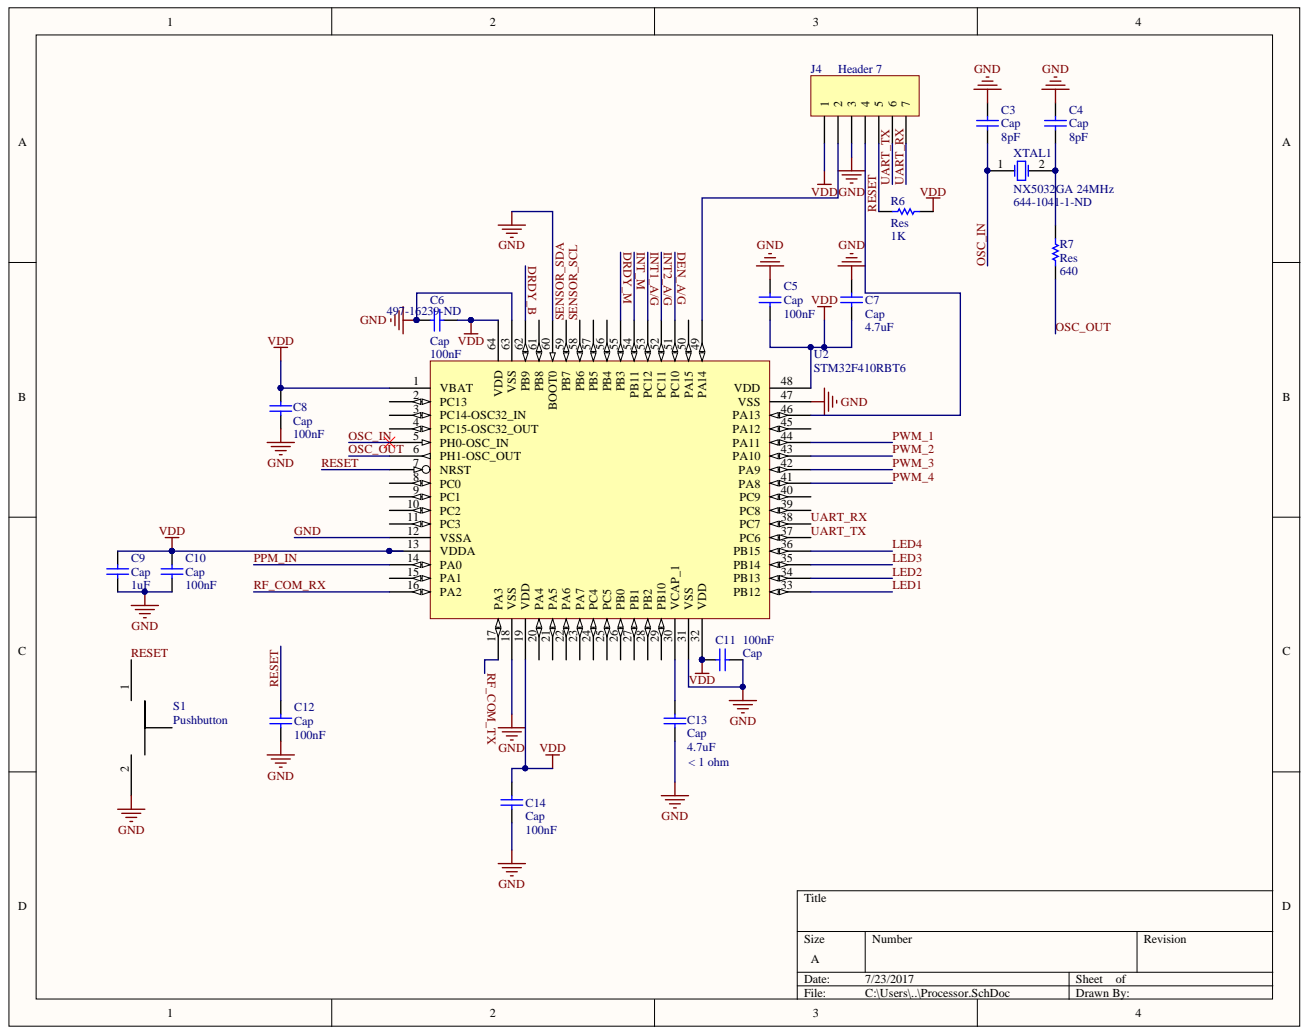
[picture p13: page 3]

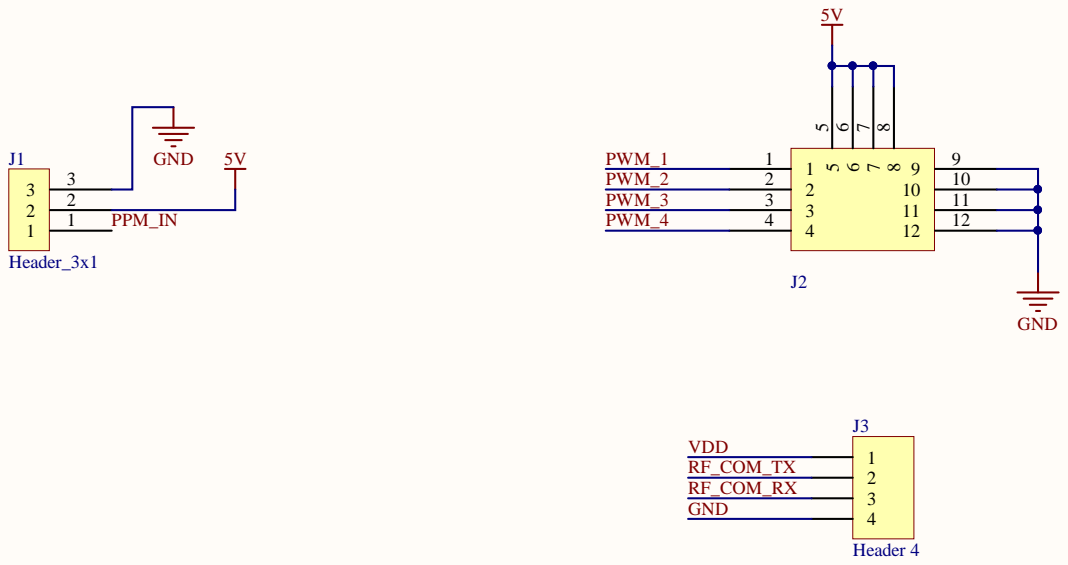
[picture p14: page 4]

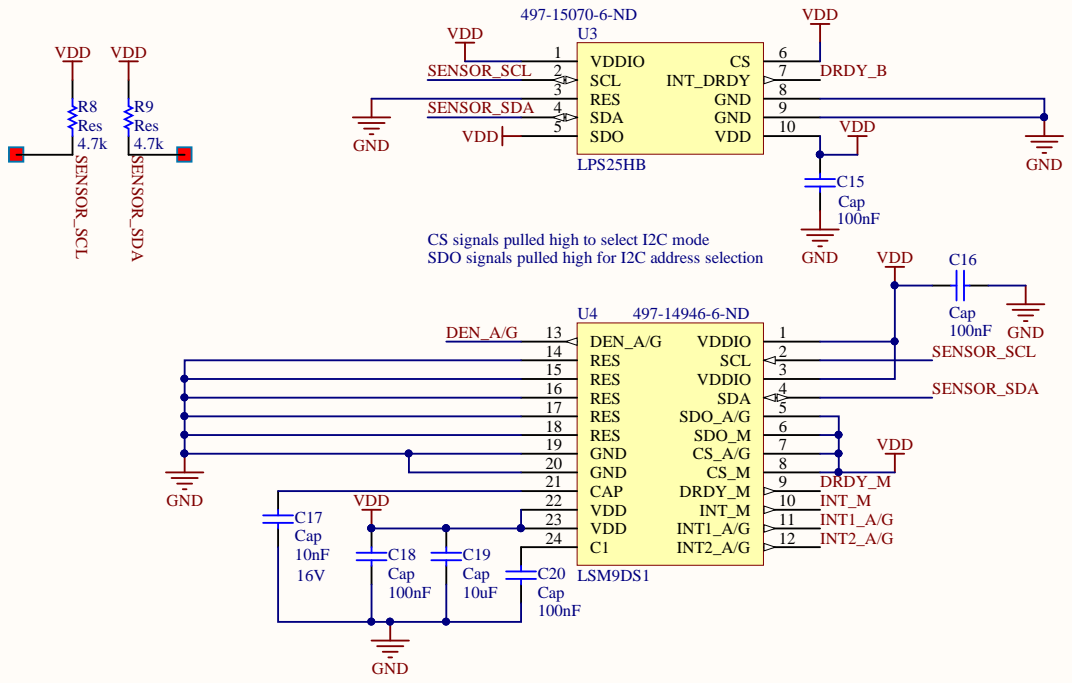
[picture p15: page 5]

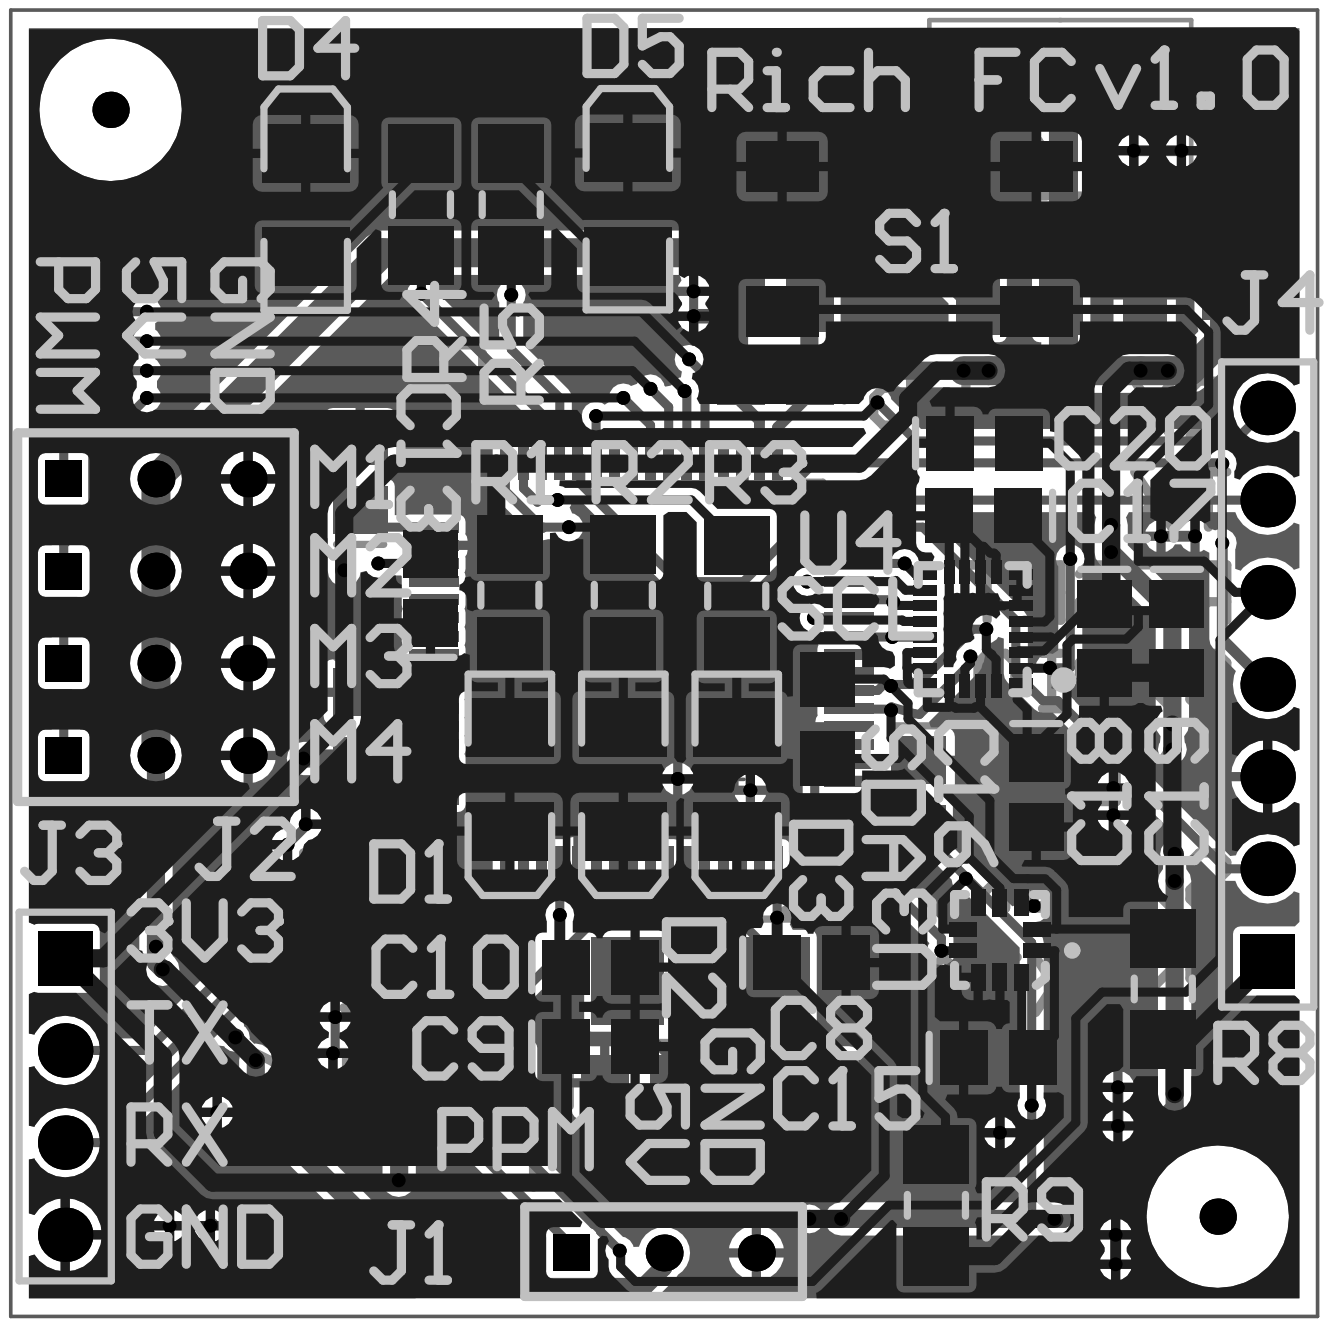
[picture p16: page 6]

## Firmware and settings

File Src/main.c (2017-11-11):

#include <stm32f4xx.h>
#include <stdbool.h>
#include <stdint.h>
#include "stdio.h"

#include "freertos.h"
#include "task.h"

#include "fc.h"
#include "main.h"
#include "hardware.h"
#include "debug.h"
#include "imu.h"
#include "pressureSensor.h"
#include "ppm.h"
#include "motors.h"
#include "controlLoop.h"

void vPrintTask1( void *pvParameters )
{
    for( ;; )
    {
        DEBUG_PRINT("Test String1\n");
        vTaskDelay(1000 / portTICK_PERIOD_MS);
    }
}
void vPrintTask2( void *pvParameters )
{
    for( ;; )
    {
        DEBUG_PRINT("Test String2\n");
        vTaskDelay(500 / portTICK_PERIOD_MS);
    }
}

void vBlinkTask( void *pvParameters )
{
    for( ;; )
    {
        rgbSetColour(RGB_GREEN);
        vTaskDelay(500 / portTICK_PERIOD_MS);
        rgbSetColour(RGB_BLUE);
        vTaskDelay(500 / portTICK_PERIOD_MS);
        rgbSetColour(RGB_RED);
        vTaskDelay(500 / portTICK_PERIOD_MS);
    }

    /* Tasks must not attempt to return from their implementing
    function or otherwise exit.  In newer FreeRTOS port
    attempting to do so will result in an configASSERT() being
    called if it is defined.  If it is necessary for a task to
    exit then have the task call vTaskDelete( NULL ) to ensure
    its exit is clean. */
    vTaskDelete( NULL );
}

void setup(void){
    // System Clock config
    ClockHSE_Config();

    // Reset of all peripherals, Initializes teh Flash interface and the Systick
    HAL_Init();

    // System interrupt init
    HAL_MspInit();

    hardware_init();

    HAL_NVIC_SetPriorityGrouping( NVIC_PRIORITYGROUP_4 ); // see http://www.freertos.org/RTOS-Cortex-M3-M4.html

    printf("Free heap size after setup: %d\n", xPortGetFreeHeapSize());

    return;
}

int main(void)
{
    setup();
    printf("System start up. Hardware initialized.\n");

    xTaskCreate(vBlinkTask, "blinkTask", 50, NULL, 2 /* priority */, NULL);
    /*xTaskCreate(vPrintTask1, "printTask1", 300, NULL, 2 [> priority <], NULL);*/
    /*xTaskCreate(vPrintTask2, "printTask2", 300, NULL, 2 [> priority <], NULL);*/
    xTaskCreate(vDebugTask, "debugTask", 300, NULL, 1 /* priority */, NULL);
    /*xTaskCreate(vPressureSensorTask, "pressureSensorTask", 300, NULL, 3 [> priority <], NULL);*/
    xTaskCreate(vIMUTask, "IMUTask", 300, NULL, 4 /* priority */, NULL);
    /*xTaskCreate(vRCTask, "RCTask", 200, NULL, 4 [> priority <], NULL);*/
    xTaskCreate(vControlLoopTask, "ControlLoopTask", 400, NULL, 3 /* priority */, NULL);

    vTaskStartScheduler();

    return 0;
}

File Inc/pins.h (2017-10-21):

#ifndef PINS_H_
#define PINS_H_

#include "stm32f4xx_hal.h"

#ifdef FC
#define LED_G_PIN GPIO_PIN_15
#define LED_G_PORT GPIOB
#define LED_R_PIN GPIO_PIN_9
#define LED_R_PORT GPIOC
#define LED_B_PIN GPIO_PIN_8
#define LED_B_PORT GPIOC

#define LED1_PIN GPIO_PIN_12
#define LED2_PIN GPIO_PIN_13
#define LED3_PIN GPIO_PIN_14
#define LED_PORT GPIOB

#define LED1_TOGGLE HAL_GPIO_TogglePin(LED_PORT, LED1_PIN);
#define LED1_ON HAL_GPIO_WritePin(LED_PORT, LED1_PIN, GPIO_PIN_SET);
#define LED1_OFF HAL_GPIO_WritePin(LED_PORT, LED1_PIN, GPIO_PIN_RESET);

#define LED2_TOGGLE HAL_GPIO_TogglePin(LED_PORT, LED2_PIN);
#define LED2_ON HAL_GPIO_WritePin(LED_PORT, LED2_PIN, GPIO_PIN_SET);
#define LED2_OFF HAL_GPIO_WritePin(LED_PORT, LED2_PIN, GPIO_PIN_RESET);

#define LED3_TOGGLE HAL_GPIO_TogglePin(LED_PORT, LED3_PIN);
#define LED3_ON HAL_GPIO_WritePin(LED_PORT, LED3_PIN, GPIO_PIN_SET);
#define LED3_OFF HAL_GPIO_WritePin(LED_PORT, LED3_PIN, GPIO_PIN_RESET);

#define MOTOR_1_PIN GPIO_PIN_11
#define MOTOR_2_PIN GPIO_PIN_10
#define MOTOR_3_PIN GPIO_PIN_9
#define MOTOR_4_PIN GPIO_PIN_8
#define MOTOR_PORT GPIOA

#elif defined(NUCLEO)
#define LED_PIN GPIO_PIN_5
#define LED_PORT GPIOA

#define LED3_PIN LED_PIN

#define LED3_TOGGLE HAL_GPIO_TogglePin(LED_PORT, LED3_PIN);
#define LED3_ON HAL_GPIO_WritePin(LED_PORT, LED3_PIN, GPIO_PIN_SET);
#define LED3_OFF HAL_GPIO_WritePin(LED_PORT, LED3_PIN, GPIO_PIN_RESET);
#endif

#endif

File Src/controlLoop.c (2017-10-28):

#include <stdbool.h>

#include "fc.h"
#include "freertos.h"
#include "task.h"

#include "ppm.h"
#include "debug.h"
#include "motors.h"
#include "rate_control.h"
#include "controlLoop.h"
#include "imu.h"

FC_Status controlLoopInit()
{
    if (motorsStart() != FC_OK) {
        // Stop any started motors
        motorsStop();
        // Delay to make sure any motors that started receive low pwm and stop spinning
        HAL_Delay(100);
        // Stop motor pwm
        motorsDeinit();
        Error_Handler("Failed to start motor output");
    }

    return FC_OK;
}

FC_Status processPpmSignal(tPpmSignal *ppmSignal, Rates_t *desiredRatesOut,
                           uint32_t *rcThrottleOut, bool *armedOut)
{
    uint32_t rcThrottle = ppmSignal->signals[THROTTLE_CHANNEL];
    rcThrottle = limit(rcThrottle, MOTOR_LOW_VAL_US, MOTOR_HIGH_VAL_US);
    (*rcThrottleOut) = rcThrottle;

    // Check if we are still armed
    // only disarm if throttle is low, so don't accidentally disarm in
    // flight
    if (ppmSignal->signals[ARMED_SWITCH_CHANNEL] >= SWITCH_HIGH_THRESHOLD) {
        (*armedOut) = true;
    } else if (ppmSignal->signals[ARMED_SWITCH_CHANNEL] <= SWITCH_LOW_THRESHOLD
               && rcThrottle <= THROTTLE_LOW_THRESHOLD ) {
        (*armedOut) = false;
    }


    /*DEBUG_PRINT("rin: %d, pin: %d, yin: %d\n", ppmSignal->signals[ROLL_CHANNEL],*/
    /*ppmSignal->signals[PITCH_CHANNEL],ppmSignal->signals[YAW_CHANNEL]);*/
    desiredRatesOut->roll = limit(map(ppmSignal->signals[ROLL_CHANNEL],
                                  MIN_RC_VAL, MAX_RC_VAL,
                                  ROTATION_AXIS_OUTPUT_MIN,
                                  ROTATION_AXIS_OUTPUT_MAX),
                              ROTATION_AXIS_OUTPUT_MIN,
                              ROTATION_AXIS_OUTPUT_MAX);
    desiredRatesOut->pitch= limit(map(ppmSignal->signals[PITCH_CHANNEL],
                                  MIN_RC_VAL, MAX_RC_VAL,
                                  ROTATION_AXIS_OUTPUT_MIN,
                                  ROTATION_AXIS_OUTPUT_MAX),
                              ROTATION_AXIS_OUTPUT_MIN,
                              ROTATION_AXIS_OUTPUT_MAX);
    desiredRatesOut->yaw= limit(map(ppmSignal->signals[YAW_CHANNEL],
                                MIN_RC_VAL, MAX_RC_VAL,
                                ROTATION_AXIS_OUTPUT_MIN,
                                ROTATION_AXIS_OUTPUT_MAX),
                            ROTATION_AXIS_OUTPUT_MIN,
                            ROTATION_AXIS_OUTPUT_MAX);
    /*DEBUG_PRINT("rd: %d, pd: %d, yd: %d\n", desiredRatesOut->roll,*/
    /*desiredRatesOut->pitch, desiredRatesOut->yaw);*/

    return FC_OK;
}

void updateMotors(uint32_t rcThrottle, RotationAxisOutputs_t *outputs)
{
    // Note that motor value limiting is done in the setMotor function
    setMotor(MOTOR_FRONT_LEFT,
             rcThrottle - outputs->roll
             + outputs->pitch
             - outputs->yaw);
    setMotor(MOTOR_BACK_LEFT,
             rcThrottle - outputs->roll
             - outputs->pitch
             + outputs->yaw);
    setMotor(MOTOR_FRONT_RIGHT,
             rcThrottle + outputs->roll
             + outputs->pitch
             + outputs->yaw);
    setMotor(MOTOR_BACK_RIGHT,
             rcThrottle + outputs->roll
             - outputs->pitch
             - outputs->yaw);
}

FC_Status checkControlLoopStatus(TickType_t lastPpmRxTime,
                                 TickType_t lastGyroRxTime,
                                 TickType_t lastLoopTime)
{
    FC_Status systemStatus = FC_OK;
    TickType_t curTick = xTaskGetTickCount();

    if (curTick - lastPpmRxTime > PPM_RX_TIMEOUT_MS)
    {
        DEBUG_PRINT("PPM timeout cur %lu last %lu\n", curTick, lastPpmRxTime);
        systemStatus = FC_ERROR;
    }
    if (curTick - lastGyroRxTime > GYRO_RX_TIMEOUT_MS)
    {
        DEBUG_PRINT("Gyro timeout cur %lu last %lu\n", curTick, lastGyroRxTime);
        systemStatus = FC_ERROR;
    }
    if (curTick - lastLoopTime > CONTROL_LOOP_TIMEOUT_MS)
    {
        DEBUG_PRINT("CtrlLp timeout cur %lu last %lu\n", curTick, lastLoopTime);
        systemStatus = FC_ERROR;
    }

    if (systemStatus != FC_OK)
    {
        // System failure, stop the motors and reset
        motorsStop();
        /*Error_Handler("system failure\n");*/
        /*while(1);*/
        NVIC_SystemReset();
    }
    else
    {
        // TODO: add wdt and kick it here
    }

    return systemStatus;
}

void vControlLoopTask(void *pvParameters)
{
    tPpmSignal ppmSignal = {0};

    bool armed = false;
    bool newGyroReceived = false;
    uint32_t rcThrottle = 1000;

    Rates_t actualRates;
    Rates_t desiredRates;
    RotationAxisOutputs_t *rotationOutputsPtr;

    DEBUG_PRINT("Control loop start\n");
    controlLoopInit();

    DEBUG_PRINT("Waiting for low throttle\n");
    // Wait for throttle to be low before continuing startup
    // This is for safety
    while (1) {
        if (xQueueReceive(ppmSignalQueue, &ppmSignal, 100) == pdTRUE) {
            rcThrottle = ppmSignal.signals[THROTTLE_CHANNEL];
            if (rcThrottle <= THROTTLE_LOW_THRESHOLD) {
                DEBUG_PRINT("Starting, thr %d\n", ppmSignal.signals[THROTTLE_CHANNEL]);
                break;
            }
        }
        vTaskDelay(PPM_FRAME_PERIOD_MS/portTICK_PERIOD_MS);
    }


    DEBUG_PRINT("Starting control loop\n");

    TickType_t lastPpmRxTime  = xTaskGetTickCount();
    TickType_t lastLoopTime   = xTaskGetTickCount();
    TickType_t lastGyroRxTime = xTaskGetTickCount();
    // This is seperate from lastLoopTime because vTaskDelayUntil sets this
    // to the last wake time + increment, even if there is some unforseen delay
    // that causes the task to miss its deadline
    TickType_t lastWakeTime   = xTaskGetTickCount();

    for ( ;; )
    {
        if (xQueueReceive(ppmSignalQueue, &ppmSignal, 0) == pdTRUE) {
            lastPpmRxTime = xTaskGetTickCount();

            if (processPpmSignal(&ppmSignal, &desiredRates,
                                 &rcThrottle, &armed) != FC_OK)
            {
                DEBUG_PRINT("Failed to process ppm signal\n");
            }
        }

        if (xQueueReceive(ratesQueue, &actualRates, 0) == pdTRUE) {
            lastGyroRxTime = xTaskGetTickCount();
            newGyroReceived = true;
        } else {
            DEBUG_PRINT("Failed to receive gyro data\n");
        }

        if (armed && rcThrottle >= THROTTLE_LOW_THRESHOLD) {
            if (newGyroReceived) {
                /*DEBUG_PRINT("ra: %d, pa: %d, ya: %d\n", actualRates.roll,*/
                /*actualRates.pitch, actualRates.yaw);*/

                rotationOutputsPtr = controlRates(&actualRates, &desiredRates);
                newGyroReceived = false;

                /*DEBUG_PRINT("ro: %d, po: %d, yo: %d\n", rotationOutputsPtr->roll,*/
                /*rotationOutputsPtr->pitch, rotationOutputsPtr->yaw);*/
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

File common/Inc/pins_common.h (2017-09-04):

/*
 * pin_common.h
 *
 *  Created on: Mar 31, 2015
 *      Author: KabooHahahein
 */

#ifndef PIN_COMMON_H_
#define PIN_COMMON_H_

#include <stm32f4xx_hal.h>

// Processor inputs
// UART
#ifdef USE_NUCLEO
#define UART_RX             GPIO_PIN_3
#define UART_TX             GPIO_PIN_2
#define UART_PORT           GPIOA
#else
#define UART_RX             GPIO_PIN_11
#define UART_TX             GPIO_PIN_10
#define UART_PORT           GPIOB
#endif

#endif /* PIN_COMMON_H_ */

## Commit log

2017-07-08 Added some I2C init and test
2017-07-10 Added generic pid control loop code along with unit test. Modified test Makefile to make adding tests easier
2017-07-10 Fix pid unitest to not use C++ extensions
2017-07-10 Changed PID struct to be multiple structs, one for gains, one for limits, and one for other values
2017-08-30 Changed I2C init to work with F4, also moved hardware setup back to hardware.c Added target option to code and makefile to specify building for FC or Nucleo
2017-09-04 Work in progress adding uart
2017-09-05 Working debug printf over uart
2017-09-05 Updated uart debugging to be thread safe by creating a queue to buffer messages and a debugging task
2017-09-07 Initial work on pressure sensor. Working whoami query
2017-09-08 Retrieving temp data from sensor
2017-09-09 Fix reg read to properly read multiple bytes
    [pressureSensor.c]
2017-09-09 Updated to switch to HSE clock after startup. Also changed error handler to use printf if the scheduler is not yet running
    [debug.c, hardware.c, main.c]
2017-09-30 Add altium design files
    [Debug.SchDoc, FC.PcbLib, FC.SchLib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]
2017-10-01 Add assert macro, update Error Handler, and add unit test for pressure sensor
    [debug.c, hardware.c, main.c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]
2017-10-01 Add more pressure sensor tests
2017-10-01 Add attitude calculation from acceleromter, and associated unit test
2017-10-06 Update unit testing to use fff mocking framework
2017-10-06 Check that pressure sensor functions access right register
2017-10-14 Added IMU registers
2017-10-15 Add debug prints on fail
    [pressureSensor.c]
2017-10-15 Add rgb led pins to pins.h
2017-10-15 Add support for RGB LED
2017-10-15 Fix some rgb led issues
    [hardware.c, main.c, pins.h]
2017-10-15 Start adding IMU support
2017-10-16 Init gyro and accel. Read acccel and scale values
2017-10-17 Add configurable scale for gyro and accel, and make sensitivity depend on scale. Also add gyro read function
2017-10-17 Add imu unit test
2017-10-17 Added semaphore to synchronize I2C bus access. Also increased I2C speed to 200kHz
2017-10-17 Changed clock config to switch to HSE clock immediately on startup. Before this happened after hardware init which caused problems.
    [hardware.c, main.c]
2017-10-18 Start adding i2c dma support
2017-10-19 Fix I2C DMA so it works. Had to fix interrupt priority to work with free rtos
    [i2c.c, imu.c, main.c]
2017-10-24 Initial control loop code. Simply pass through throttle val. There is a bug in the ppm code that seems to output 1000us at max throttle.
    [controlLoop.c, hardware.c, main.c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]
2017-10-24 Limit throttle output to motor controllers
2017-10-26 Fixes so code compiles for unit tests
    [imu.c]
2017-10-26 Added control loop status check that checks for timeouts in receiving ppm data, gyro data, or overall loop time. Also modified scheduling to use vTaskDelayUntil for better periodic execution accuracy
2017-10-26 Increase motor output frequency to 490 Hz
2017-10-26 Fixes so code compiles
    [controlLoop.c, imu.c]
2017-10-27 Fixed system status checking, and fixed integrated error calculation
    [controlLoop.c]
2017-10-28 Attempt to add i2c reinit routine, not sure if works but maybe this will fix i2c busy errors. Also change system status check to restart system on failure
    [controlLoop.c, i2c.c, i2c.h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]
2017-10-28 Update altium files to latest version
    [Debug.SchDoc, FC.PcbLib, FC.SchLib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]
2017-10-29 Change gyro bandwidth to set gyro lpg to 100Hz
2017-10-30 Start adding filter functions to be used in the control loop
2017-11-11 Fix some filter stuff
2017-11-11 Fix filter so it compiles, still not used though
2017-11-19 Add board render pictures
2017-11-26 Move invert pitch and yaw axis to imu driver code
    [imu.c]
